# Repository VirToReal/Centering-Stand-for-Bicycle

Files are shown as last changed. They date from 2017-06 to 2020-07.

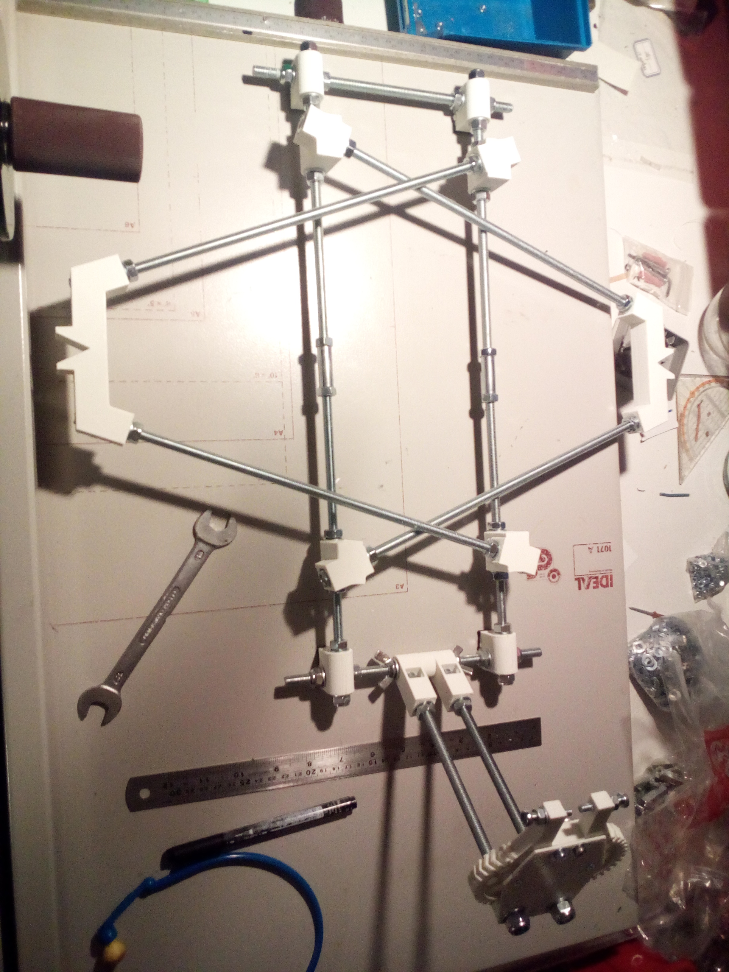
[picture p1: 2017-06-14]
Images/Centering_Stand_3.jpg

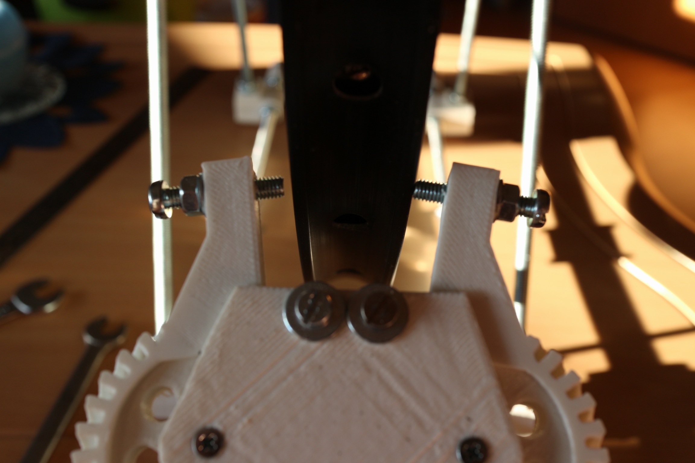
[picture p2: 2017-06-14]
Images/Centering_Stand_2.jpg

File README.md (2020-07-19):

ATTENTION
============
I moved my repositories to gitlab, please do any suggestions there: https://gitlab.com/Hirmer/Centering-Stand-for-Bicycle

Thank you!

# Centering-Stand-for-Bicycle
Zentrierständer für Fahrrad-Laufräder / Centering-Stand for Bicycle-Impeller

Fully parametric with OpenSCAD ("Zentrierstaender.scad" + "gears-helical.scad")

Thingiverse-Link with same Files (https://www.thingiverse.com/thing:2385150)
Helical Gear by Catarina Mota (https://www.thingiverse.com/thing:1339)

# INFORMATION - CONSTRUCTING
Add the Parameters to fit the size of your wheel. You can be clumsy with that,
because the turquoise colored rods in the OpenScad-Preview are threaded-rods
and can be easily adjusted to your needed distances. Because of that, better
give some more than having to less at the end.

The variable "printmode" help you switch between OpenSCAD-Preview and Printmode.
The Preview shows your Adjustments on the Parameters. The "printmode = true" with
it's following variables will prepare a print-ready layout of your parametered
Structures. The length of each (not printable) Threaded-Rod will be "echoed" in the
OpenSCAD-Console. They can be cut in exact that length.

Following things have to be considered while building:
- RIM-GRABBER:
- All other small holes can be drilled up to 4mm for 20mm long M4 Screws to
assemble the whole Rim-Grabber altogether.

- You have to pull a shell with the length of 10.15mm inside the two gears
The Diameter of the shell should match the size of appr. 5-5.9mm, it doesn't
have to be exact that size, tolerance to the Hole in the Gear is desirable.
You have to drill up the Hole in the Gears up to appr. 6mm too, because your
printer won't work that exactly. For Example: I used 2x 3mm² end sleeves which
fits perfectly.

There must fit a 3mm Screw inside that shell to fix these two gears together
with fewer tolerances. Be sure the screws just fix the shell with the other
two structures (cap/baseplate), not the gears! Some grease will help, too!
The two arms of the Grabber should touch in the center before mounting.
You can rotate them altogether to fix them afterwards. Just be sure they're
in the right teeth of the gear. ITS IMPORTANT THAT THESE GEARS HAVE NO
TOLERANCES TO EACH OTHER.

- The two big holes are for the Threaded Rods. They're also fixing the "cap"
on the "baseplate" with the Gears between them.

- Cut a thread into the two Grabber-Arms for M5-Screws and place some inside
them. They should look out the structure the same distance. If you failed
with assembling the Grabber-Arms correctly, you can adjust here.

ALL OTHER PARTS:
- Not much to consider, just use Nut-Traps if there are one. Washers may prevent
the plastic from damage. Locknuts on some points may help against self adjusting.
The OpenSCAD Preview with "printmode = false" may explain everything to you.

# INFORMATION - USING
Consider following things before start working with this tool:
- Be sure to tighten the Axis by clamping them in with the two Impeller-Holder.

- You have to measure in your Rim first before start working on it. You're able
to rearrange the "Rim-Grabber" on the Threaded Rod for this.

- If all Threaded Rods are tightened, the whole Structures may move during work
on your rim, but they'll always move back in they're original position. The
position will stay the same even after reinserting the rim after removal.

- You'll detect the wrong position by the sound when the rim touches one of the screws.
Measuring right at the Rim-Grabber makes it easy to adjust the spokelength. Always Adjust
3 spokes before/after the one with the strongest swing to get a smoother result.
You're also be able to add a metal-plate to detect runouts of the rim. Just use the
upper two screws of the Rim-Grabber to mount one.

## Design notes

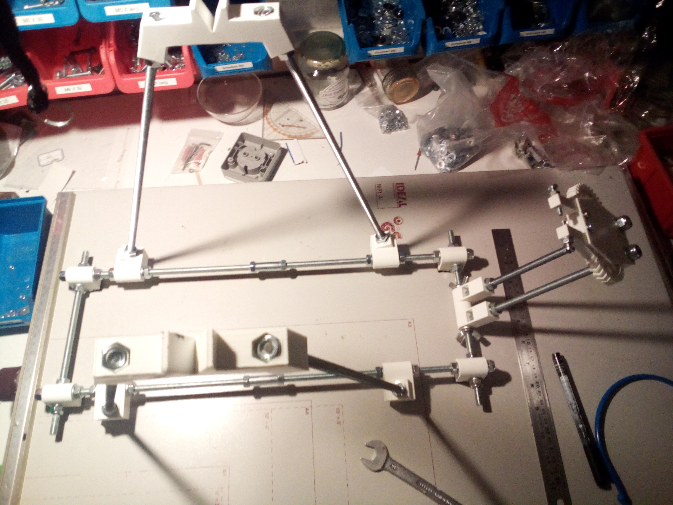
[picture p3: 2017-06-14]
Images/Centering_Stand_4.jpg

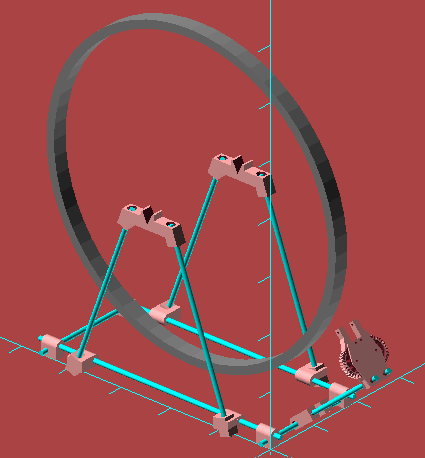
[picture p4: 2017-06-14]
Images/Centering_Stand_6.png

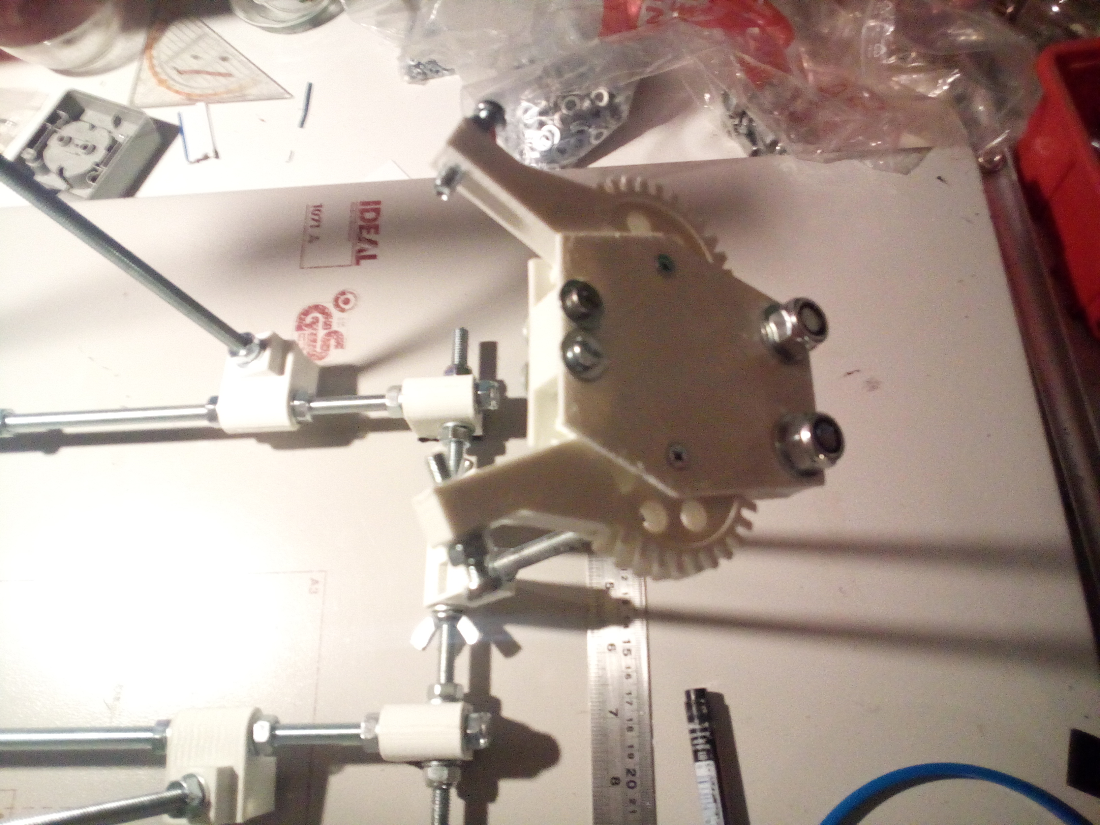
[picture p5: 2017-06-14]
Images/Centering_Stand_5.jpg

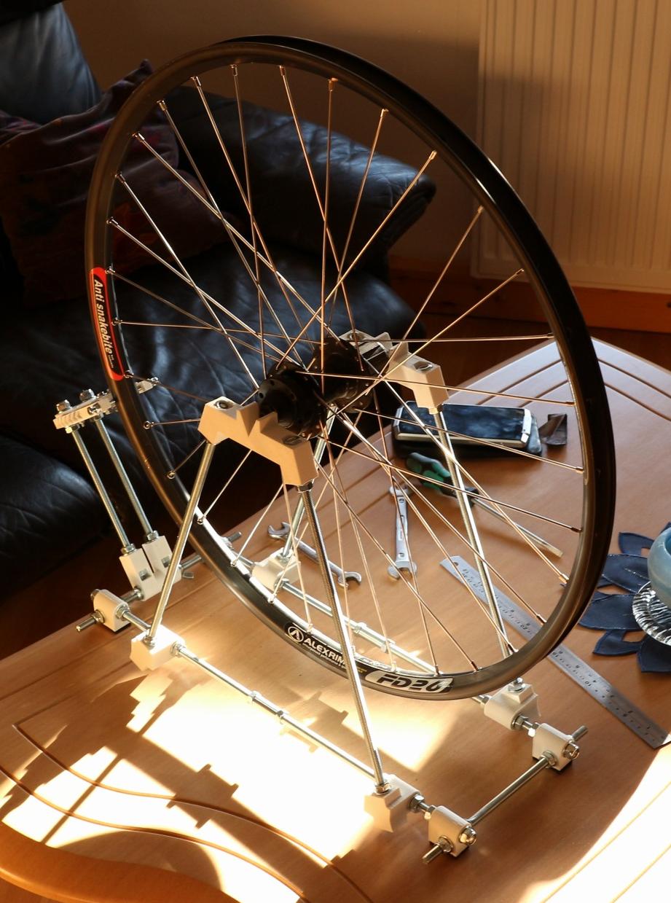
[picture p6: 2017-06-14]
Images/Centering_Stand_1.jpg

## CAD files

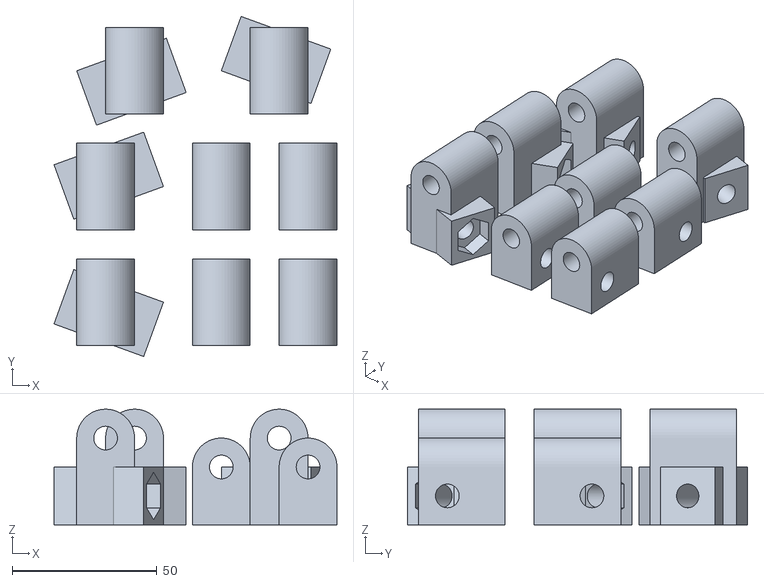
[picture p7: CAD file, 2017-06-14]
Zentrierstaender_Feets.stl
97.9 x 117.6 x 40.0

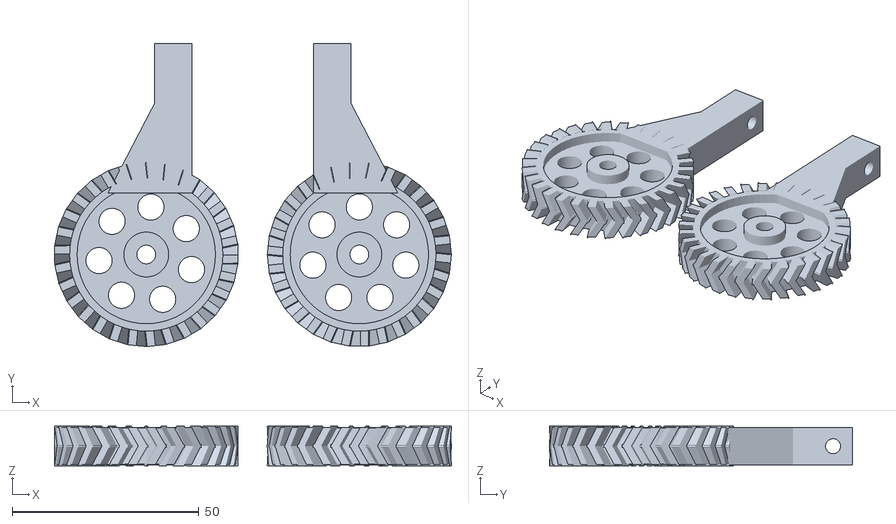
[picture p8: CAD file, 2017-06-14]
Zentrierstaender_Grabber.stl
106.2 x 81.2 x 10.7

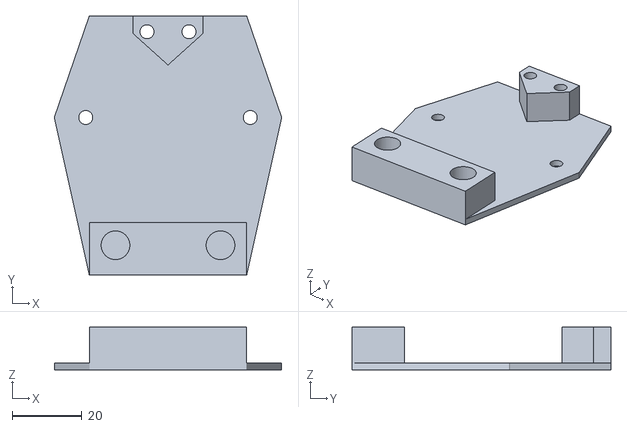
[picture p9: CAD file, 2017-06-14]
Zentrierstaender_Baseplate.stl
65.0 x 74.0 x 12.2

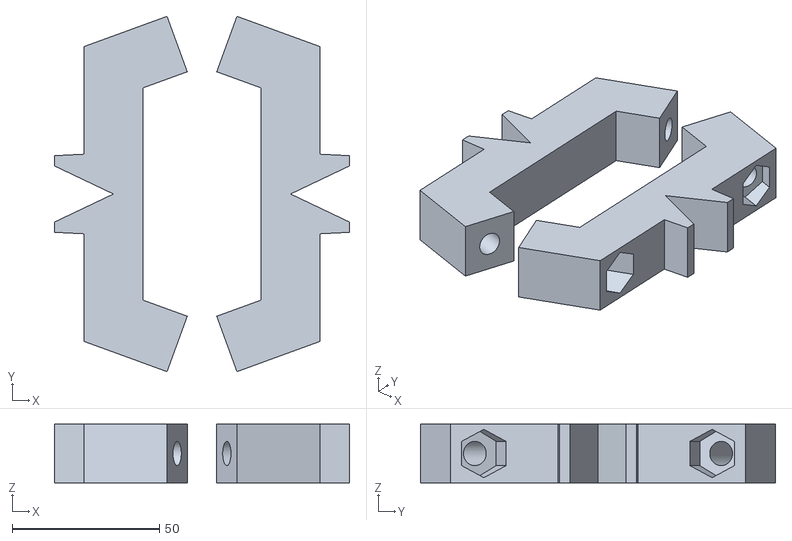
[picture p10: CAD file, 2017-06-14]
Zentrierstaender_Steg.stl
100.1 x 120.5 x 20.0

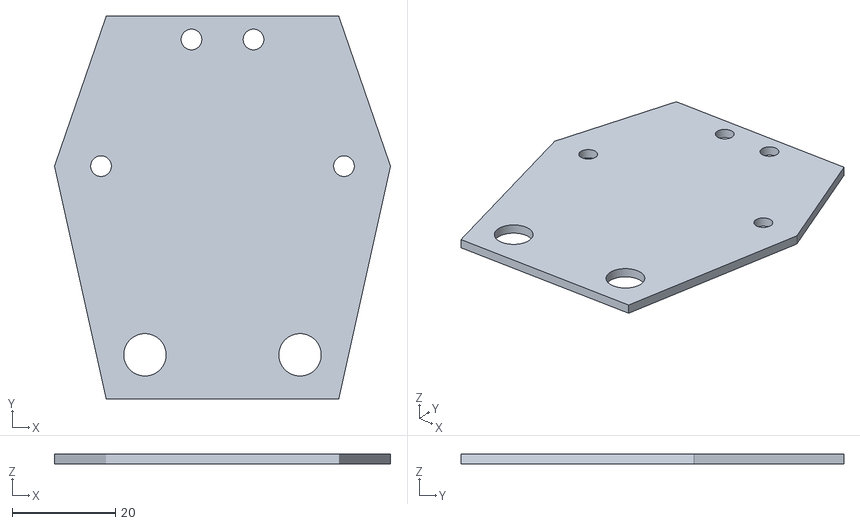
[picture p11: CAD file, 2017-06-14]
Zentrierstaender_Cap.stl
65.0 x 74.0 x 2.00

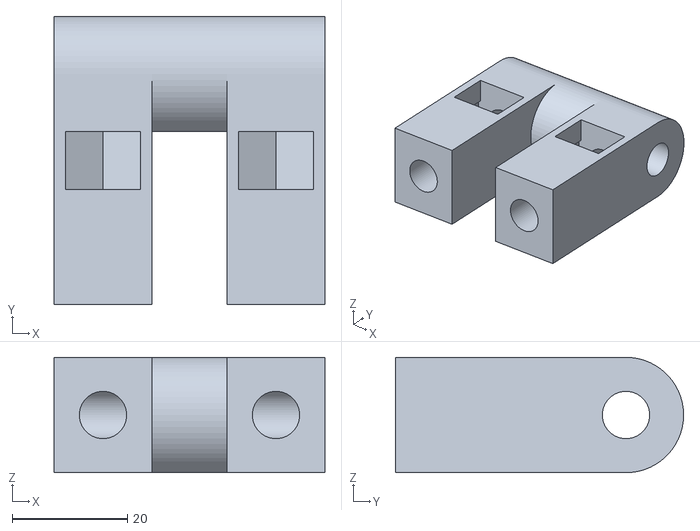
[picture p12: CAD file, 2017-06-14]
Zentrierstaender_Holder.stl
47.0 x 50.0 x 20.0

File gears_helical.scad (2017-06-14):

// Helical Gears
// Catarina Mota
// catarinamfmota@gmail.com
// 20091123


//GEAR PARAMETERS
doubleHelical=1; //int: 0=no, 1=yes (will make the gear 2x taller)

gearHeight=5; //gear depth

pitchDiam=45; //pitch diameter

shaftDiam=5; //shaft diameter

//TEETH PARAMETERS
teethNum=30; //number of teeth (int)

addendum=2;

dedendum=2;

toothWidth=2;

angle=-30; //positive=right, negative=left

orientation=-1; //int: 1=left, -1=right

//CENTER SHAPE PARAMETERS
centerShape=3; //int: solid=1, star=2, circle=3

starNum=6; //number of lines for star shape (int)
starWidth=2; //width of star lines

circleNum=7; //number of circles (int)
circleDiam=7; //diameter of circles

//CENTER CIRCLE PARAMETERS
extrudeOut=1; //int: 0=no, 1=yes
extrudeOutHeight=3;
extrudeOutWidth=7; //in relationship to shaft

extrudeIn=1; //int: 0=no, 1=yes
extrudeInDiam=pitchDiam/2-dedendum*2;
extrudeInHeight=3;

//ROME (extrudeIn must be set to 0)
rome=0; //int: 0=no, 1=yes
romeDiam=pitchDiam/2; //pitch diameter for top gear
romeHeight=gearHeight; //top gear height
romeTeeth=teethNum*2/3;
romeAdd=2; //top gear addendum
romeDed=2; //top gear dedendum
romeToothWidth=2; //teeth width for top gear
romeAngle=5; //rotate top gear (angle)

//----------------------



//----------------------

//TOOTH
module tooth(heightGear, diamPitch) {

	toothHeight=addendum+dedendum*2;

	union(){
		translate([0,toothHeight/2,0]) rotateTooth(1);
		if (doubleHelical==1){
			translate([0,toothHeight/2,-heightGear+0.1]) rotateTooth(-1);
		}
	}

	module rotateTooth(direction){
		difference(){
			rotate([0,direction*angle,0])
			box(toothWidth,toothHeight,heightGear*1.5);

			translate([0,0,heightGear*0.75+dedendum/2])
			box(heightGear,toothHeight+0.5,dedendum+heightGear/2);

			translate([0,0,-heightGear*0.75-dedendum/2])
			box(heightGear,toothHeight+0.5,dedendum+heightGear/2);
		}
	}
}



//HELICAL
module helical(numTeeth, diamPitch, heightGear) {
	rootRad=diamPitch/2-dedendum;
	difference(){
	for (i = [1:numTeeth]) {
		translate([sin(360*i/numTeeth)*(rootRad-dedendum), cos(360*i/numTeeth)*(rootRad-dedendum), 0 ]){
			rotate([0,0,-360*i/numTeeth]) tooth(heightGear, diamPitch);
		}
	}
	translate([0,0,-gearHeight/2-1]) cylinder(heightGear+2, diamPitch/2-dedendum, diamPitch/2-dedendum);
	}
}

//SOLID
module solid(heightGear, diamPitch) {
	rootRad=diamPitch/2-dedendum;
	translate([0,0,-(heightGear*doubleHelical)+0.1*doubleHelical])
	cylinder(heightGear+(heightGear-0.1)*doubleHelical, rootRad, rootRad);
}

//STAR
module star() {
	starAngle=360/starNum;
	rootRad=diamPitch/2-dedendum;
	union(){
		for (s=[1:starNum]){
			translate([0,0,gearHeight/2-(gearHeight/2*doubleHelical)]){
				rotate([0, 0, s*starAngle]) dislocateBox(starWidth, (pitchDiam/2-dedendum*2)/2, gearHeight+(gearHeight*doubleHelical));
			}
		}
		translate ([0,0,-gearHeight*doubleHelical])
		tube(gearHeight+(gearHeight*doubleHelical), pitchDiam/2-dedendum, starWidth);
		translate ([0,0,-gearHeight*doubleHelical]){
			tube(gearHeight+(gearHeight*doubleHelical), pitchDiam/4+dedendum, starWidth);
			//cylinder(gearHeight+(gearHeight*doubleHelical), pitchDiam/4+dedendum, pitchDiam/4+dedendum);
		}
		translate([0,0,-gearHeight*doubleHelical])
		cylinder(gearHeight+(gearHeight*doubleHelical), shaftDiam/2+starWidth, shaftDiam/2+starWidth);
	}
}

//CIRCLE
module circle() {
	rootRad=pitchDiam/2-dedendum;
	difference(){
		solid(gearHeight-0.1*doubleHelical, pitchDiam);
		for (c=[1:circleNum]){
			translate([sin(360*c/circleNum)*(rootRad/2+shaftDiam/2), cos(360*c/circleNum)*(rootRad/2+shaftDiam/2), -gearHeight*doubleHelical]){
				cylinder(gearHeight+gearHeight*doubleHelical, circleDiam/2, circleDiam/2);
			}
		}
	}
}

//ROME
module romeGear(){
	translate([0,0,romeHeight/2+gearHeight]){
		rotate([0,0,romeAngle]){
			union(){
				helical(romeTeeth, romeDiam, romeHeight);
				translate ([0,0,-romeHeight/2]) solid(romeHeight, romeDiam);
			}
		}
	}
}

//GEAR
module gear(){

	difference () {

		union() {
			translate([0,0,gearHeight/2]) helical(teethNum, pitchDiam, gearHeight);

			if (centerShape==1) solid(gearHeight, pitchDiam);

			if (centerShape==2) star();

			if (centerShape==3) circle();

			if (rome==1) romeGear();

			//extrudeOut around shaft
			if (extrudeOut==1) {
translate([0,0,-gearHeight*doubleHelical+0.1*doubleHelical])	cylinder(gearHeight-(extrudeInHeight*extrudeIn)+extrudeOutHeight+romeHeight*rome+gearHeight*doubleHelical-0.1*doubleHelical, extrudeOutWidth/2+shaftDiam/2, extrudeOutWidth/2+shaftDiam/2);
			}

		}

	//extrudeIn around shaft
		if (extrudeIn==1) {
			difference(){
				translate([0,0,gearHeight-extrudeInHeight+0.1*doubleHelical]) cylinder(extrudeInHeight, extrudeInDiam, extrudeInDiam);
				cylinder(gearHeight+extrudeOutHeight, (extrudeOutWidth+shaftDiam)/2*extrudeOut, (extrudeOutWidth+shaftDiam)/2*extrudeOut);
			}
		}

	//shaft
	translate([0,0,-gearHeight*doubleHelical]) cylinder(gearHeight+extrudeOutHeight+romeHeight+(gearHeight*doubleHelical), shaftDiam/2, shaftDiam/2);
	}
}

//----------------------

//SILLY WAY TO GET AROUND ROTATION AXIS

module dislocateBox(xBox, yBox, zBox){
	translate([0,yBox,0]){
		difference(){
			box(xBox, yBox*2, zBox);
			translate([-xBox,0,0]) box(xBox, yBox*2, zBox);
		}
	}
}

//----------------------

module box(xBox, yBox, zBox) {
	scale ([xBox, yBox, zBox]) cube(1, true);
}

module cone(height, radius) {
		cylinder(height, radius, 0);
}

module oval(xOval, yOval, zOval) {
	scale ([xOval/100, yOval/100, 1]) cylinder(zOval, 50, 50);
}

module tube(height, radius, wall) {
	difference(){
		cylinder(height, radius, radius);
		cylinder(height, radius-wall, radius-wall);
	}
}

module hexagon(height, depth) {
	boxWidth=height/1.75;
		union(){
			box(boxWidth, height, depth);
			rotate([0,0,60]) box(boxWidth, height, depth);
			rotate([0,0,-60]) box(boxWidth, height, depth);
		}
}

module octagon(height, depth) {
	intersection(){
		box(height, height, depth);
		rotate([0,0,45]) box(height, height, depth);
	}
}

module dodecagon(height, depth) {
	intersection(){
		hexagon(height, depth);
		rotate([0,0,90]) hexagon(height, depth);
	}
}

module hexagram(height, depth) {
	boxWidth=height/1.75;
	intersection(){
		box(height, boxWidth, depth);
		rotate([0,0,60]) box(height, boxWidth, depth);
	}
	intersection(){
		box(height, boxWidth, depth);
		rotate([0,0,-60]) box(height, boxWidth, depth);
	}
	intersection(){
		rotate([0,0,60]) box(height, boxWidth, depth);
		rotate([0,0,-60]) box(height, boxWidth, depth);
	}
}

module rightTriangle(adjacent, opposite, depth) {
	difference(){
		translate([-adjacent/2,opposite/2,0]) box(adjacent, opposite, depth);
		translate([-adjacent,0,0]){
			rotate([0,0,atan(opposite/adjacent)]) dislocateBox(adjacent*2, opposite, depth);
		}
	}
}

module equiTriangle(side, depth) {
	difference(){
		translate([-side/2,side/2,0]) box(side, side, depth);
		rotate([0,0,30]) dislocateBox(side*2, side, depth);
		translate([-side,0,0]){
			rotate([0,0,60]) dislocateBox(side*2, side, depth);
		}
	}
}

module 12ptStar(height, depth) {
	starNum=3;
	starAngle=360/starNum;
	for (s=[1:starNum]){
		rotate([0, 0, s*starAngle]) box(height, height, depth);
	}
}

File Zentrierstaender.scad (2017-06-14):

/*
Zentrierständer für Fahrrad-Laufräder / Centering-Stand for Bicycle-Impeller
Copyright (C) 2017  Benjamin Hirmer - hardy at virtoreal.net
This program is free software: you can redistribute it and/or modify
it under the terms of the GNU General Public License as published by
the Free Software Foundation, either version 3 of the License, or
(at your option) any later version.
This program is distributed in the hope that it will be useful,
but WITHOUT ANY WARRANTY; without even the implied warranty of
MERCHANTABILITY or FITNESS FOR A PARTICULAR PURPOSE.  See the
GNU General Public License for more details.
You should have received a copy of the GNU General Public License
along with this program.  If not, see <http://www.gnu.org/licenses/>.
*/


/*
######### INFORMATION - CONSTRUCTING #########
Add the Parameters to fit the size of your wheel. You can be clumsy with that,
because the turquoise colored rods in the OpenScad-Preview are threaded-rods
and can be easily adjusted to your needed distances. Because of that, better
give some more than having to less at the end.

The variable "printmode" help you switch between OpenSCAD-Preview and Printmode.
The Preview shows your Adjustments on the Parameters. The "printmode = true" with
it's following variables will prepare a print-ready layout of your parametered
Structures. The length of each (not printable) Threaded-Rod will be "echoed" in the
OpenSCAD-Console. They can be cut in exact that length.

Following things have to be considered while building:
- RIM-GRABBER:
- All other small holes can be drilled up to 4mm for 20mm long M4 Screws to
assemble the whole Rim-Grabber altogether.

- You have to pull a shell with the length of 10.15mm inside the two gears
The Diameter of the shell should match the size of appr. 5-5.9mm, it doesn't
have to be exact that size, tolerance to the Hole in the Gear is desirable.
You have to drill up the Hole in the Gears up to appr. 6mm too, because your
printer won't work that exactly. For Example: I used 2x 3mm² end sleeves which
fits perfectly.

There must fit a 3mm Screw inside that shell to fix these two gears together
with fewer tolerances. Be sure the screws just fix the shell with the other
two structures (cap/baseplate), not the gears! Some grease will help, too!
The two arms of the Grabber should touch in the center before mounting.
You can rotate them altogether to fix them afterwards. Just be sure they're
in the right teeth of the gear. ITS IMPORTANT THAT THESE GEARS HAVE NO
TOLERANCES TO EACH OTHER.

- The two big holes are for the Threaded Rods. They're also fixing the "cap"
on the "baseplate" with the Gears between them.

- Cut a thread into the two Grabber-Arms for M5-Screws and place some inside
them. They should look out the structure the same distance. If you failed
with assembling the Grabber-Arms correctly, you can adjust here.

ALL OTHER PARTS:
- Not much to consider, just use Nut-Traps if there are one. Washers may prevent
the plastic from damage. Locknuts on some points may help against self adjusting.
The OpenSCAD Preview with "printmode = false" may explain everything to you.


######### INFORMATION - USING #########
Consider following things before start working with this tool:
- Be sure to tighten the Axis by clamping them in with the two Impeller-Holder.

- You have to measure in your Rim first before start working on it. You're able
to rearrange the "Rim-Grabber" on the Threaded Rod for this.

- If all Threaded Rods are tightened, the whole Structures may move during work
on your rim, but they'll always move back in they're original position. The
position will stay the same even after reinserting the rim after removal.

- You'll detect the wrong position by the sound when the rim touches one of the screws.
Measuring right at the Rim-Grabber makes it easy to adjust the spokelength. Always Adjust
3 spokes before/after the one with the strongest swing to get a smoother result.
You're also be able to add a metal-plate to detect runouts of the rim. Just use the
upper two screws of the Rim-Grabber to mount one.

*/

// Parameters
$fn = 60; // Model Resolution of Round Objects
aotr = 12; //Add of Threaded Rod at the ends for Nuts and Spacers
dotn = 13; //Diameter of the Nut for the Threaded Rods (8mm Threaded-Rods need 13mm)

dbfw = 150; // Distance between feets (width) (minimum the lenght of your beared axis)
dbfl = 400; // Distance between feets (length) (see how it works out for you in the OpenSCAD-Preview)
robw = 580; // Diameter of Bike-Wheel (add some tollerances, maybe you want to calibrate different tires)

footjoint_width = 20; // Width of Global Structures (check if the Nut-Traps have enough space)
footjoint_length = 30; // Length of Global Structures
footjoint_thrededrod = 8.2; // Threaded Rod Diameter - to join the Structures together (add some tollerances)

impellerholder_angle = 70; // Degree of Impeller-Holder (leave some space on the length-side, add some "dbfl" if you have to, so you can rearrange the whole wheel if you have to)
impellerholder_width = 100; // Upper Steg Length
impellerholder_rabbetd = 20; // Depth of Rabbet of Tire-Axis (your Axis should fit in it)
impellerholder_rabbetw = 20; // Width of Rabbet of Tire-Axis (your Axis should fit in it)

rimgrabber_distance = 200; // Distance Away from the Frame (play with the distance and armlength to find a nice working position for your rim)
rimgrabber_armlength = 40; // Length of the Grabber-Arms
rimgrabber_angle = 40; // Angle of Rim-Grabber (just for Simulation)

// Print Parts / Show Mounted Structure
printmode = true;

// Print Part # (15x Parts Total)
printfeeds = false; // Print all Feeds (8x Parts)
printfeeds_sb = 10; // Distance between Feeds
printstege = false; // Print the two Stege (2x Parts)
printrimgrabber_p1 = false; // Print the Rim-Grabber - Part 1 (Gearset) (2x Parts)
printrimgrabber_p2 = false; // Print the Rim-Grabber - Part 2 (Cap) (1x Part)
printrimgrabber_p3 = true; // Print the Rim-Grabber - Part 3 (Baseplate) (1x Part)
printrimgrabber_p4 = false; // Print the Holder of the Rim-Grabber (1x Part)


// Import Catarina Mota's Helical Gears (https://www.thingiverse.com/thing:1339)
include <gears_helical.scad>;

module trod (length, rotationx, rotationy, rotationz, diameter) { // Simulated Threaded-Rod
    color ("Aqua") rotate (a=[rotationx,rotationy,rotationz]) cylinder (h = length, r = diameter/2);
}

module footjoint (width, length, threadedrod) { // Foot for the Frame of the Stand
    difference () {
        union () {
            cube ( size = [width,length,width]); // Body
            translate ([width/2,0,width]) rotate ([-90,0,0]) cylinder ( h = length, r = width/2); // Body-Top
        }
        translate ([-1,width/2,width/2]) rotate ([0,90.0]) cylinder ( h = width+2, r = threadedrod/2 ); // Threaded Rod Width
        translate ([width/2,-1,width]) rotate ([-90,0.0]) cylinder ( h = length+2, r = threadedrod/2 ); // Threaded Rod Length
    }

}

module impellerholder (width, length, threadedrod, angle, dotn) { // Feed for Steg
    nutdia = dotn/2/cos(180/6)+0.7;
    difference () {
        union () {
            translate ([-width,0,width/2]) cube ( size = [width+width/2,length,width] );
            translate ([width/2,0,width]) rotate ([-90,0,0]) cylinder ( h = length, r = width/2 );
            translate ([-width,length/2,0]) rotate ([angle,0,0]) cube ( size = [width,length*1.1,width] );
        }
        union () {
            translate ([width/2,-1,width]) rotate ([-90,0,0]) cylinder ( h = length+2, r = threadedrod/2 ); // Threaded Rod
            translate ([-width/2,length/2-((width/2)/cos(-90+angle)),0]) rotate ([-90+angle,0,0]) cylinder ( h = length*2+2, r = threadedrod/2 ); // Threaded Rod
            translate ([-width/2,length/2-((width/2)/cos(-90+angle)),0]) rotate ([-90+angle,0,0]) cylinder ($fn = 6, r = nutdia, h = 10); // Nut Trap
        }
    }
}
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
